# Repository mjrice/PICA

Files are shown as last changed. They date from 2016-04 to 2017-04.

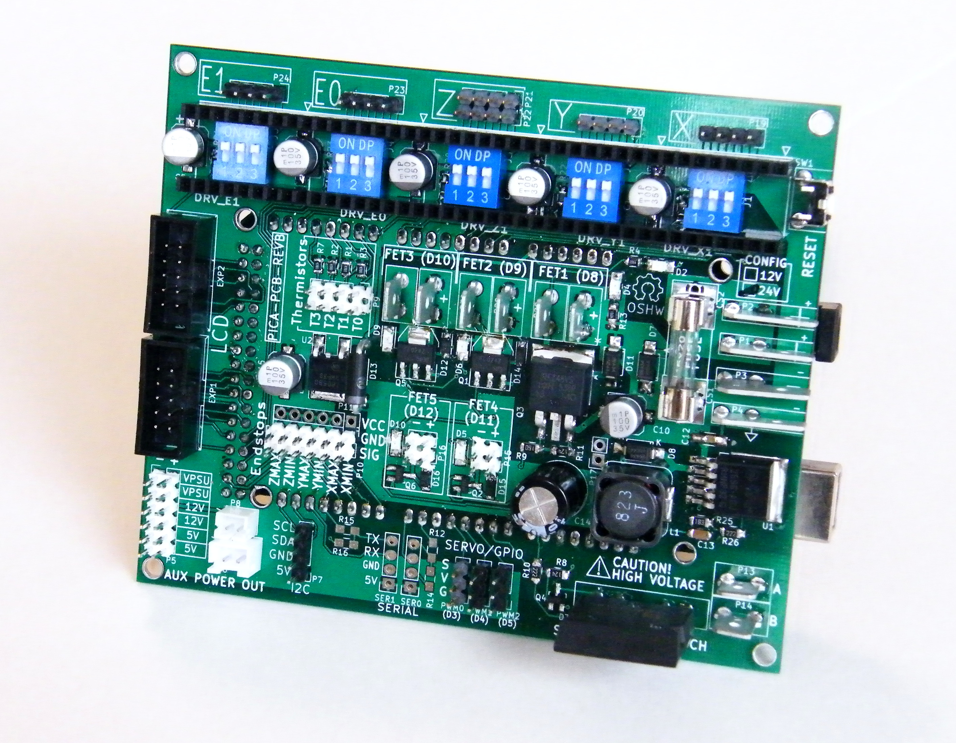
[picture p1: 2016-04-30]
pica-assembled-24v.jpg

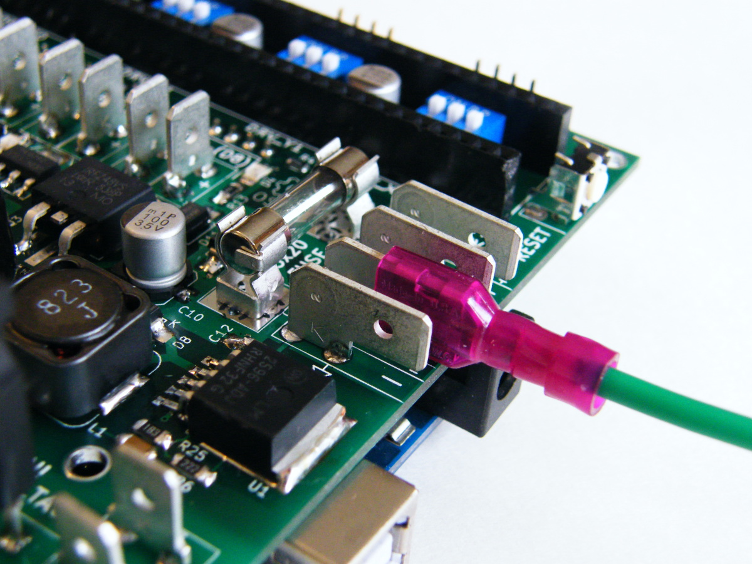
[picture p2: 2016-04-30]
qc.jpg

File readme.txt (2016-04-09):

PICA

Power, Interface, and Control Adapter

An Arduino Mega shield for reprap machines

Based in part on RAMPS by Johnny Russell

Power

* 5x20mm replaceable fuse input 

* 12V to 24V input with on-board 12V buck converter for systems with both 24V and 12V devices

* Five separate MOSFET outputs:

1 High power (15A, up to 24V)
2 Medium power (6A, up to 24V)
2 Low power (2A, 12V)

* Plus 1 SSR output (SPST) capable of 240VAC/5A (more with heatsink)

Monitoring 

* four thermistor inputs
* six endstop inputs

Interface

* LCD interface (SMART LCD controller pinout)
* I2C, 2xSerial, 3xPWM, and auxiliary DC power output connections
* Five Pololu stepper motor driver sockets (A4988 or DRV8825)

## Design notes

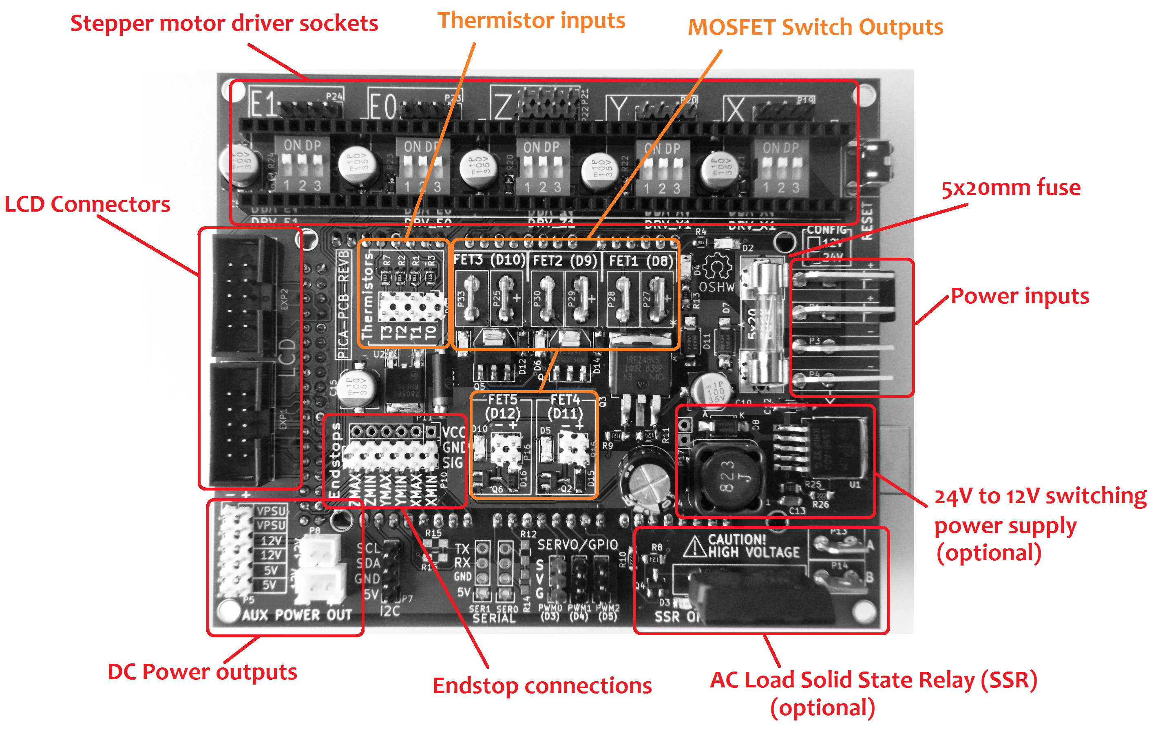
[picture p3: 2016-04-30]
pica-design-layout.png

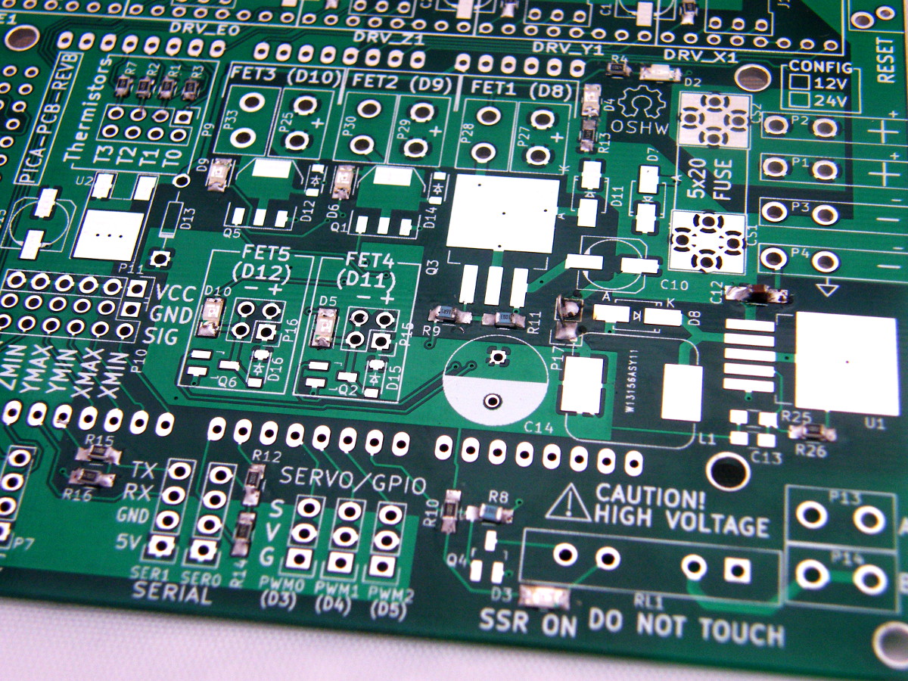
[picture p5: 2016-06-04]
r2k_100k.jpg

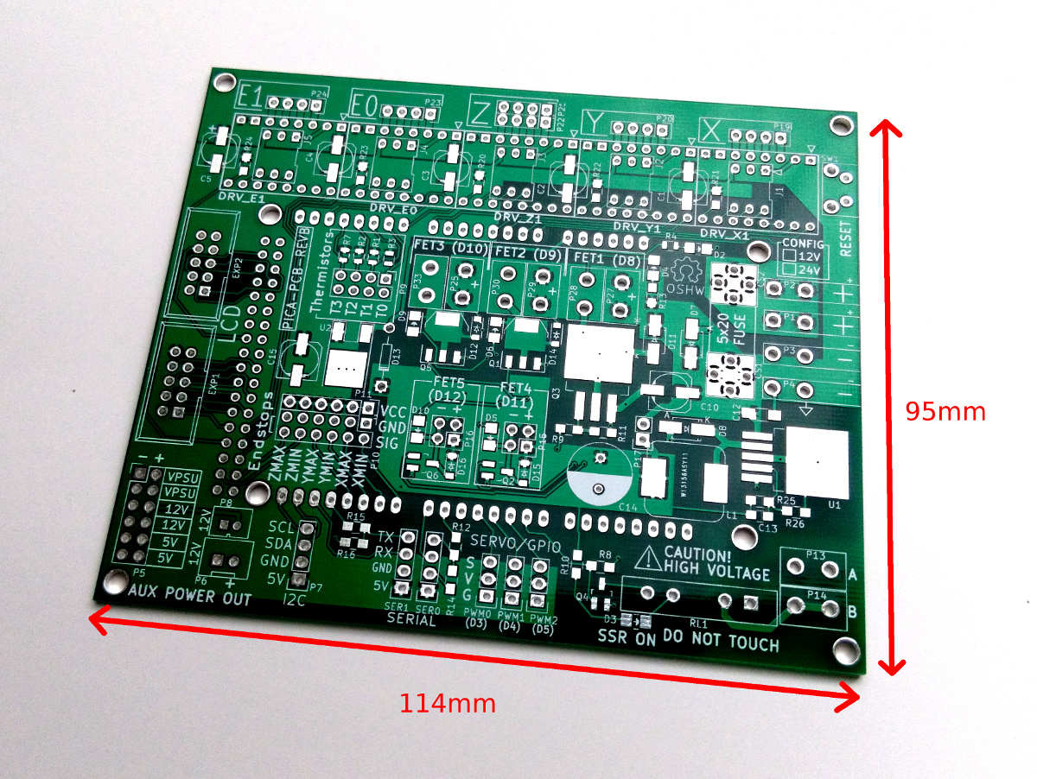
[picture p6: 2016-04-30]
pica-pcb-photo.jpg

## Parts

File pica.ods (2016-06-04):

Parts list, in the recommended order of assembly
Designator | Package | Quantity | Designation | KIT BAG
R13,R20,R21,R22,R23,R24,R14,R16,R4,R5,R6,R1,R2,R3,R7 | R_0805_HandSoldering | 15 | 4.7K | 1
D2 | LED_1206 | 1 | GREEN
D4,D5,D6,D9,D10,D3 | LED_1206 | 6 | Led_Small
RP1 | RESARY_4_CTS_744 | 1 | YC164-JR-0722RL
RP3 | RESARY_4_CTS_744 | 1 | YC164-JR-073K3L
RP2 | RESARY_4_CTS_744 | 1 | YC164-JR-07100KL
 |  |  |  | 2
C6,C7,C8,C9,C11,C12 | C_0805_HandSoldering | 6 | .1UF
R26,R10,R12,R15 | R_0805_HandSoldering | 4 | 2K
R11,R8 | R_0805_HandSoldering | 2 | 100K
 |  |  |  | 3
R9 | R_0805_HandSoldering | 1 | 10
D16,D12,D15,D14 | SOD-123 | 4 | MBR0560
D7,D11 | SMA_Handsoldering | 2 | SS36
 |  |  |  | 4
Q2,Q4,Q6 | SOT-23_Handsoldering | 3 | IRLML6346
Q1,Q5 | SOT-223 | 2 | IRFL024ZPbF
Q3 | TO-263-3Lead | 1 | IRFZ48VS
 |  |  |  | 5
U2 | TO-252-2Lead | 1 | MC7805BDTRKG
C10,C15,C1,C2,C3,C4,C5 | c_elec_6.3x5.8 | 7 | 100UF
J1,J2,J3,J4,J5 | DIP-6_0_ELL | 5 | CONN_02X03
 |  |  |  | 6
DRV_Z1,DRV_X1,DRV_E1,DRV_E0,DRV_Y1 | SWDIP8_.6W | 5 | POLOLU_A4988
EXP1,EXP2 | IDC_Header_Straight_10pins | 2 | CONN_02X05
P11 | Pin_Header_Straight_1x06 | 1 | CONN_01X06
P10,P5 | Pin_Header_Straight_2x06 | 2 | CONN_02X06
P7,P19,P20,P21,P22,P23,P24 | Pin_Header_Straight_1x04 | 7 | CONN_01X04
P9 | Pin_Header_Straight_2x04 | 1 | CONN_02X04
PWM0,PWM1,PWM2 | Pin_Header_Straight_1x03 | 3 | CONN_01X03
P15,P16 | Pin_Header_Straight_1x02 | 2 | CONN_02X02
 |  |  |  | 7
SER0,SER1 | Pin header (female) | 2 | CONN_01X04
SW1 | BSF_RT | 1 | BSF-3100
P17 | Jumper wire | 1
D13 | Diode_Horizontal | 1 | 1N5333
CS1,CS2 | FUSE_CLIP_D_5x20 | 2 | FUSE_CLIP_5x20
P8, P12, P18 | JST_PH_2POS | 3 | JST-PH
P6 | JST_XH_2POS | 1 | JST-XH
SHIELD1 | MEGA_NOLINES | 1 | ARDUINO_MEGA_SHIELD
P28,P27,P29,P30,P25,P33,P13,P14 | SPACE_CONN_VERT | 8 | CONN_01X02 | 8
P2,P1,P3,P4 | SPADE_CONN_RT | 4 | 36-4966-ND

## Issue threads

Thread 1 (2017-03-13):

PICA 24V parts list; Re-ARM compatibility: bridge Vpsu/12V to Vin?

rumlyne, 2017-03-13:
Dear mjrice,

searching for a better alternative than a 24V RAMPS for my Re-ARM board I came across your PICA and I have a few questions:
Are you selling a set of the components needed to make it 24V compatible? If not could you provide a parts list?
Also the PICA provides the Arduino Mega with 9V via the Vin pin. The Re-ARM needs at least 10V and can tolerate up to 30V. Is there a way to bridge that pin to Vpsu/24V or 12V on the Pico? What other electronic parts does the PICOs 9V regulator supply with current? If there are no others it should be easy to bridge the pads reserved for that regulator.

Best regards,
rumlyne

rumlyne, 2017-04-18:
He replied on a different platform:

I sell the boards with or without the 24V input. When it is installed, it
is a buck converter that generates an on-board 12V from the 24V. The 12V
is used to power the two lower power mosfet switches as well as the
on-board 5V regulator and the arduino itself through a zener diode. The
three higher power mosfet switches and the stepper motor drivers are driven
from the input supply directly. You can also modify a 12V unit to be 24V
compatible - the design is all open source and the schematic is here:
https://github.com/mjrice/PICA/blob/master/pica_schematic.pdf

And lastly to answer your question, yes, you could either short out or
reverse the diode D13 which would increase the voltage on the arduino's VIN
pin from 9V to about 11.3V.

I don't know much about the Re-arm board but otherwise it looks like it
should work like you expect.

Closed 2017-04-18.

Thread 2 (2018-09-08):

No 5V (VCC) on the shield

Duckle29, 2018-09-08:
Hey there. I'm flipping through the board and schematic (in kicad) and I can't figure out where the shield gets 5v from

It seems that the shields 12v is separate from U2, which should generate the onboard 5v. The only way I can see this working, is if the arduino is powered through it's barrel-jack, and then this voltage is passed to the shield via the megas VIN pin, why not use the on-board 12v source, or at least offer a power selector jumper?

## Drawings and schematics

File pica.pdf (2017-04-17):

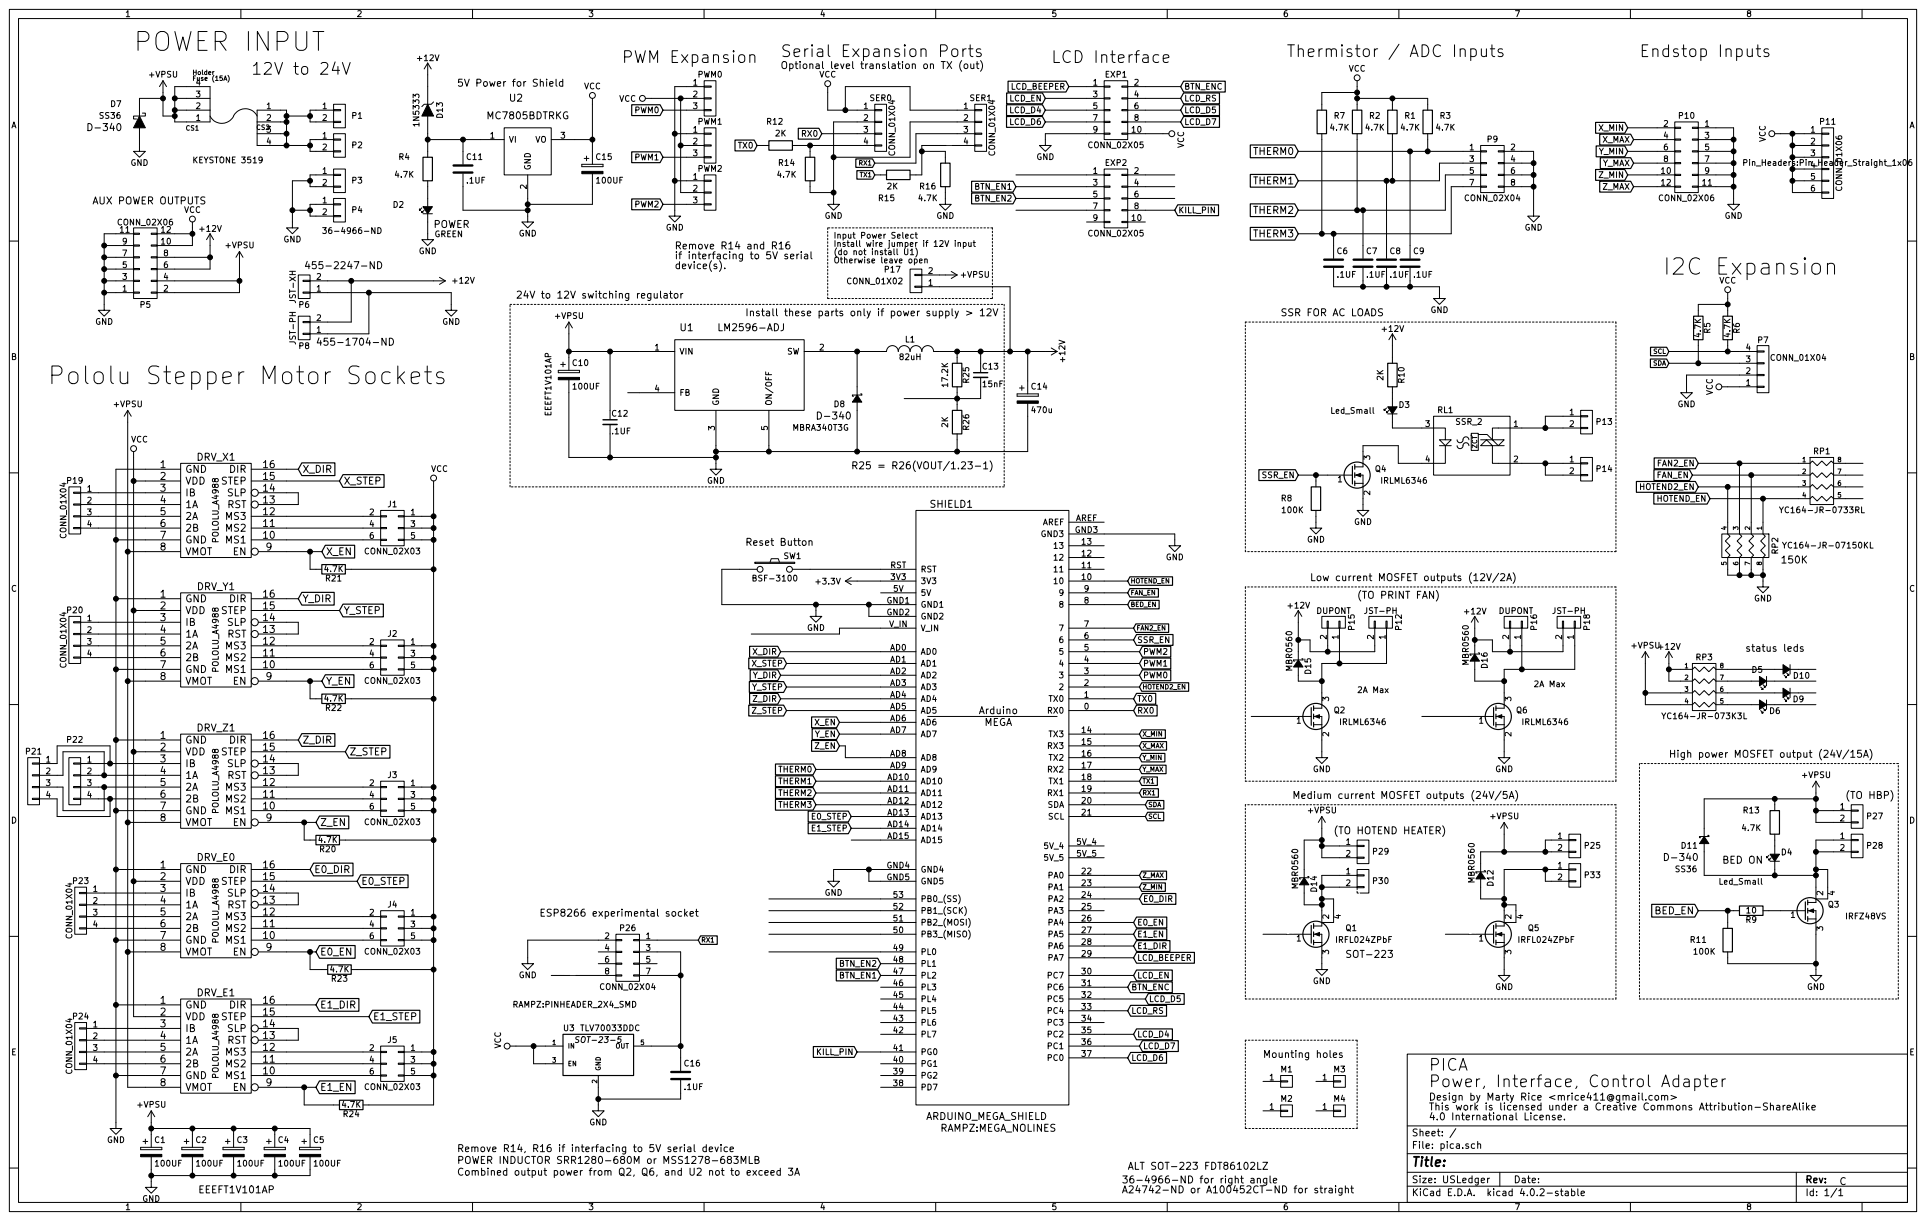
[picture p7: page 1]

+3.3V Serial Expansion Ports
4.7KGND Optional level translation on TX (out)
3PWM0 GND

Input Power Select
Install wire jumper if 12V input
(do not install U1)

if interfacing to 5V serial

status leds 24V to 12V switching regulator

Install these parts only if power supply > 12V

4 RL1 SSR_2 D3 Led_Small SSR FOR AC LOADS

Pololu Stepper Motor Sockets

High power MOSFET output (24V/15A) 150K

Medium current MOSFET outputs (24V/5A)

PICA
Power, Interface, Control Adapter
Design by Marty Rice <mrice411@gmail.com>
This work is licensed under a Creative Commons Attribution-ShareAlike 4.0 International License.

File: pica.sch Sheet: /

Remove R14, R16 if interfacing to 5V serial device
POWER INDUCTOR SRR1280-680M or MSS1278-683MLB
Combined output power from Q2, Q6, and U2 not to exceed 3A

ALT SOT-223 FDT86102LZ
36-4966-ND for right angle
A24742-ND or A100452CT-ND for straight

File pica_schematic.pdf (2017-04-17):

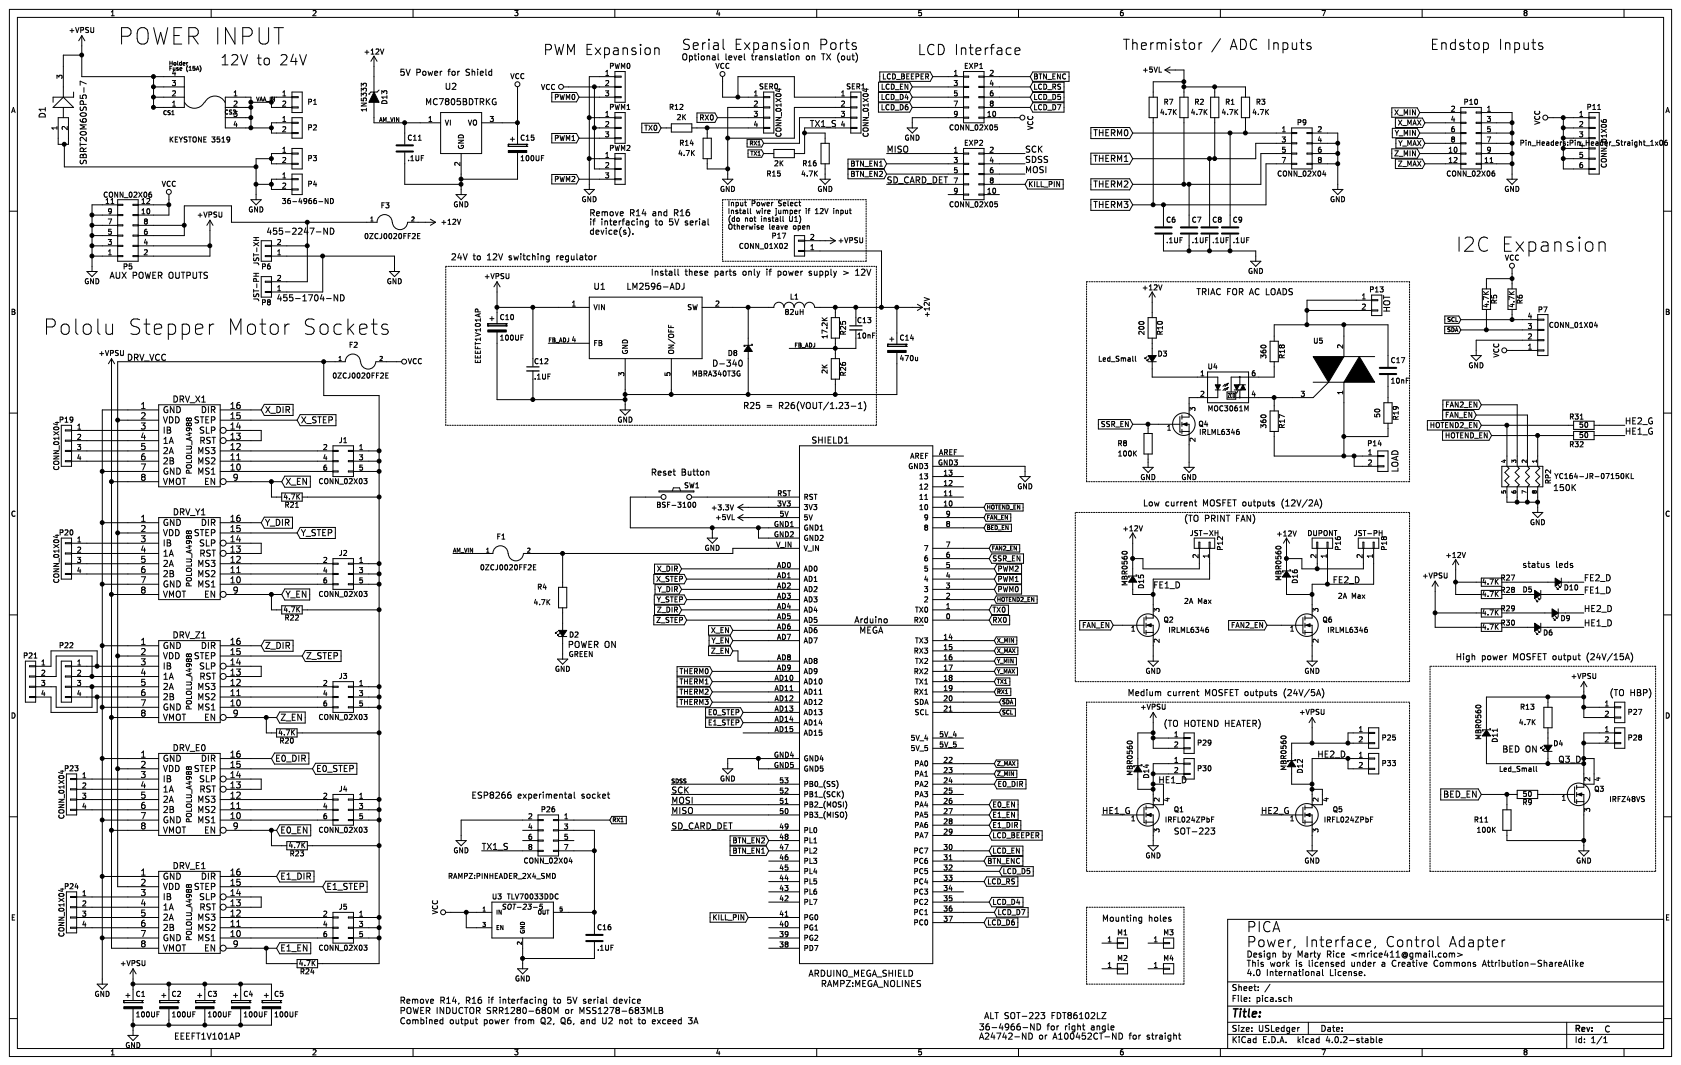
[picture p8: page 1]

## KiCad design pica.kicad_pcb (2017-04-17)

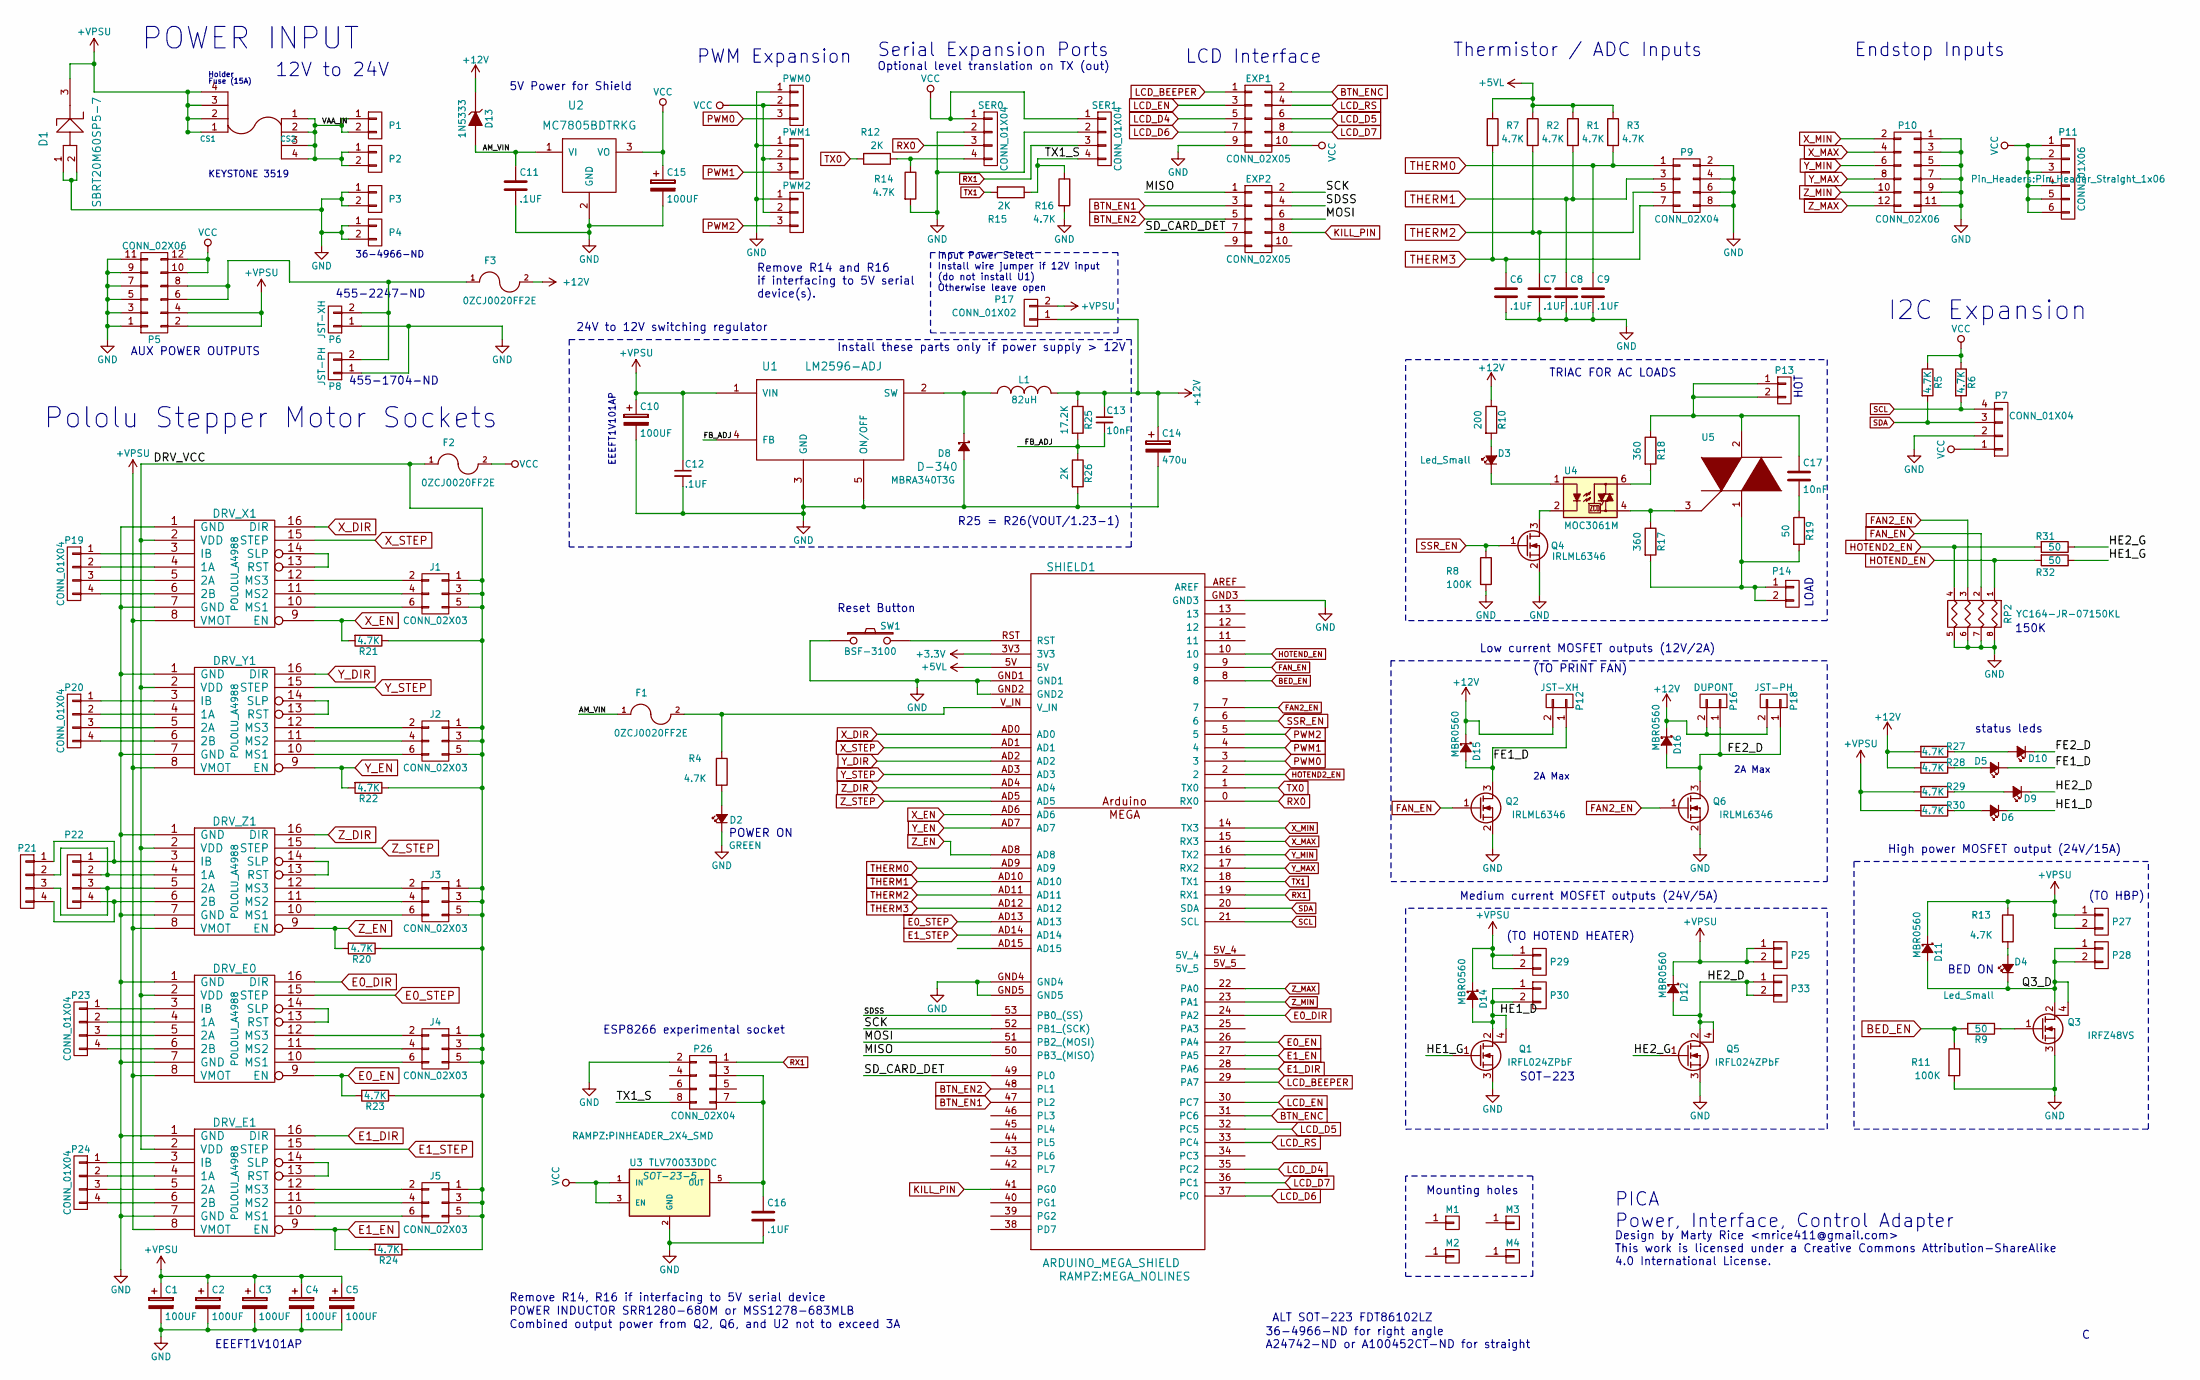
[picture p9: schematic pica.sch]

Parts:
C1, C2, C3, C4, C5, C10, C15: 100UF; c_elec_6.3x5.8
C6, C7, C8, C9, C11, C12, C16: .1UF; C_0805_HandSoldering
C13, C17: 10nF; C_1206_HandSoldering
C14: 470u; C_Radial_D10_L13_P5
CS1, CS2: FUSE_CLIP_5x20; FUSE_CLIP_D_5x20
D1: SBRT20M60SP5-7; POWERDI5
D2: GREEN; LED_1206
D3, D4, D5, D6, D9, D10: Led_Small; LED_1206
D8: MBRA340T3G; SMA_Handsoldering
D11, D12, D14, D15, D16: MBR0560; SOD-123
D13: 1N5333; Diode_Horizontal
DRV_E0, DRV_E1: POLOLU_A4988; SWDIP8_.6W
DRV_X1: POLOLU_A4988; SWDIP8_.6W
DRV_Y1: POLOLU_A4988; SWDIP8_.6W
DRV_Z1: POLOLU_A4988; SWDIP8_.6W
EXP1, EXP2: CONN_02X05; IDC_Header_Straight_10pins_DUAL
F1, F2, F3: 0ZCJ0020FF2E; Fuse_SMD1206_Wave
J1, J2, J3, J4, J5: CONN_02X03; DIP-6_0_ELL
L1: 82uH; RH127
M1, M2, M3, M4: CONN_01X01; MHOLE125
P1, P2, P3, P4: 36-4966-ND; SPADE_CONN_RT
P5, P10: CONN_02X06; Pin_Header_Straight_2x06
P6, P12: JST-XH; JST_XH_2POS
P7, P19, P20, P21, P22, P23, P24: CONN_01X04; Pin_Header_Straight_1x04
P8, P18: JST-PH; JST_PH_2POS
P9: CONN_02X04; Pin_Header_Straight_2x04
P11: CONN_01X06; Pin_Header_Straight_1x06
P13, P14, P25, P27, P28, P29, P30, P33: CONN_01X02; SPACE_CONN_VERT
P16: DUPONT; Pin_Header_Straight_1x02
P17: CONN_01X02; Pin_Header_Straight_1x02
P26: CONN_02X04; PINHEADER_2X4_SMD
PWM0, PWM1, PWM2: CONN_01X03; Pin_Header_Straight_1x03
Q1, Q5: IRFL024ZPbF; SOT-223
Q2, Q4, Q6: IRLML6346; SOT-23_Handsoldering
Q3: IRFZ48VS; TO-263-3Lead
R1, R2, R3, R4, R5, R6, R7, R13, R14, R16, R20, R21, R22, R23, R24, R27, R28, R29, R30: 4.7K; R_0805_HandSoldering
R8, R11: 100K; R_0805_HandSoldering
R9, R19, R31, R32: 50; R_0805_HandSoldering
R10: 200; R_0805_HandSoldering
R12, R15, R26: 2K; R_0805_HandSoldering
R17, R18: 360; R_0805_HandSoldering
R25: 17.2K; R_0805_HandSoldering
RP2: YC164-JR-07150KL; RESARY_4_CTS_744
SER0, SER1: CONN_01X04; Pin_Header_Straight_1x04
SHIELD1: ARDUINO_MEGA_SHIELD; MEGA_NOLINES
SW1: BSF-3100; BSF_RT
U1: LM2596-ADJ; TO-263-5Lead
U2: MC7805BDTRKG; TO-252-2Lead
U3: TLV70033DDC; SOT-23-5
U4: MOC3061M; 6SMD
U5: TRIAC; TO-252-2Lead

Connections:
+3V3: SHIELD1.3V3
+5VL: R1.1, R2.1, R3.1, R7.1, SHIELD1.5V
+12V: C13.1, C14.1, D13.1 (K), D15.1 (K), D16.1 (K), F3.2, L1.2, P12.2, P16.2, P17.1, P18.2, R10.1, R25.1, R27.2, R28.2
+VPSU: C1.1, C2.1, C3.1, C4.1, C5.1, C10.1, C12.1, CS1.1, CS1.2, CS1.3, CS1.4, D1.3, D11.1 (K), D12.1 (K), D14.1 (K), DRV_E0.8 (VMOT), DRV_E1.8 (VMOT), DRV_X1.8 (VMOT), DRV_Y1.8 (VMOT), DRV_Z1.8 (VMOT), P5.2, P5.4, P17.2, P25.1, P25.2, P27.1, P27.2, P29.1, P29.2, R13.1, R29.2, R30.2, U1.1 (VIN)
/AM_VIN: C11.1, D13.2 (A), F1.1, U2.1 (VI)
/DRV_VCC: DRV_E0.2 (VDD), DRV_E1.2 (VDD), DRV_X1.2 (VDD), DRV_Y1.2 (VDD), DRV_Z1.2 (VDD), F2.1, J1.1, J1.3, J1.5, J2.1, J2.3, J2.5, J3.1, J3.3, J3.5, J4.1, J4.3, J4.5, J5.1, J5.3, J5.5, R20.1, R21.1, R22.1, R23.1, R24.1
/FB_ADJ: C13.2, R25.2, R26.1, U1.4 (FB)
/FE1_D: D5.1 (K), D15.2 (A), P12.1, Q2.3 (D)
/FE2_D: D10.1 (K), D16.2 (A), P16.1, P18.1, Q6.3 (D)
/HE1_D: D6.1 (K), D14.2 (A), P30.1, P30.2, Q1.2 (D), Q1.4 (D)
/HE1_G: Q1.1 (G), R32.1
/HE2_D: D9.1 (K), D12.2 (A), P33.1, P33.2, Q5.2 (D), Q5.4 (D)
/HE2_G: Q5.1 (G), R31.1
/MISO: EXP2.1, SHIELD1.50 (PB3_(MISO))
/MOSI: EXP2.6, SHIELD1.51 (PB2_(MOSI))
/Q3_D: D4.1 (K), D11.2 (A), P28.1, P28.2, Q3.2 (D), Q3.4 (D)
/SCK: EXP2.2, SHIELD1.52 (PB1_(SCK))
/SDSS: EXP2.4, SHIELD1.53 (PB0_(SS))
/SD_CARD_DET: EXP2.7, SHIELD1.49 (PL0)
/TX1_S: P26.8, R15.1, R16.1, SER1.4
/VAA_IN: CS2.1, CS2.2, CS2.3, CS2.4, P1.1, P1.2, P2.1, P2.2
BED_EN: R9.2, R11.1, SHIELD1.8
BTN_EN1: EXP2.3, SHIELD1.47 (PL2)
BTN_EN2: EXP2.5, SHIELD1.48 (PL1)
BTN_ENC: EXP1.2, SHIELD1.31 (PC6)
E0_DIR: DRV_E0.16 (DIR), SHIELD1.24 (PA2)
E0_EN: DRV_E0.9 (EN), R23.2, SHIELD1.26 (PA4)
E0_STEP: DRV_E0.15 (STEP), SHIELD1.AD13
E1_DIR: DRV_E1.16 (DIR), SHIELD1.28 (PA6)
E1_EN: DRV_E1.9 (EN), R24.2, SHIELD1.27 (PA5)
E1_STEP: DRV_E1.15 (STEP), SHIELD1.AD14
FAN2_EN: Q6.1 (G), RP2.3, SHIELD1.7
FAN_EN: Q2.1 (G), RP2.2, SHIELD1.9
GND: C1.2, C2.2, C3.2, C4.2, C5.2, C6.2, C7.2, C8.2, C9.2, C10.2, C11.2, C12.2, C14.2, C15.2, C16.2, D1.1, D1.2, D2.1 (K), D8.2 (A), DRV_E0.1 (GND), DRV_E0.7 (GND), DRV_E1.1 (GND), DRV_E1.7 (GND), DRV_X1.1 (GND), DRV_X1.7 (GND), DRV_Y1.1 (GND), DRV_Y1.7 (GND), DRV_Z1.1 (GND), DRV_Z1.7 (GND), EXP1.9, P3.1, P3.2, P4.1, P4.2, P5.1, P5.3, P5.5, P5.7, P5.9, P5.11, P6.1, P7.2, P8.1, P9.2, P9.4, P9.6, P9.8, P10.1, P10.3, P10.5, P10.7, P10.9, P10.11, P26.2, PWM0.1, PWM1.1, PWM2.1, Q1.3 (S), Q2.2 (S), Q3.3 (S), Q4.2 (S), Q5.3 (S), Q6.2 (S), R8.2, R11.2, R14.2, R16.2, R26.2, RP2.5 (R4), RP2.6 (R3), RP2.7 (R2), RP2.8 (R1), SER0.2, SER1.2, SHIELD1.GND1, SHIELD1.GND2, SHIELD1.GND3, SHIELD1.GND4, SHIELD1.GND5, SW1.1, U1.3 (GND), U1.5 (ON/OFF), U2.2 (GND), U3.2 (GND)
HOTEND2_EN: R31.2, RP2.4, SHIELD1.2
HOTEND_EN: R32.2, RP2.1, SHIELD1.10
KILL_PIN: EXP2.8, SHIELD1.41 (PG0)
LCD_BEEPER: EXP1.1, SHIELD1.29 (PA7)
LCD_D4: EXP1.5, SHIELD1.35 (PC2)
LCD_D5: EXP1.6, SHIELD1.32 (PC5)
LCD_D6: EXP1.7, SHIELD1.37 (PC0)
LCD_D7: EXP1.8, SHIELD1.36 (PC1)
LCD_EN: EXP1.3, SHIELD1.30 (PC7)
LCD_RS: EXP1.4, SHIELD1.33 (PC4)
unnamed: C16.1, P26.3, P26.7, U3.5 (OUT)
unnamed: C17.1, P13.1, P13.2, R18.1, U5.2
unnamed: C17.2, R19.1
unnamed: D2.2 (A), R4.2
unnamed: D3.1 (K), U4.1
unnamed: D3.2 (A), R10.2
unnamed: D4.2 (A), R13.2
unnamed: D5.2 (A), R28.1
unnamed: D6.2 (A), R30.1
unnamed: D8.1 (K), L1.1, U1.2 (SW)
unnamed: D9.2 (A), R29.1
unnamed: D10.2 (A), R27.1
unnamed: DRV_E0.3 (IB), P23.1
unnamed: DRV_E0.4 (1A), P23.2
unnamed: DRV_E0.5 (2A), P23.3
unnamed: DRV_E0.6 (2B), P23.4
unnamed: DRV_E0.10 (MS1), J4.6
unnamed: DRV_E0.11 (MS2), J4.4
unnamed: DRV_E0.12 (MS3), J4.2
unnamed: DRV_E0.13 (RST), DRV_E0.14 (SLP)
unnamed: DRV_E1.3 (IB), P24.1
unnamed: DRV_E1.4 (1A), P24.2
unnamed: DRV_E1.5 (2A), P24.3
unnamed: DRV_E1.6 (2B), P24.4
unnamed: DRV_E1.10 (MS1), J5.6
unnamed: DRV_E1.11 (MS2), J5.4
unnamed: DRV_E1.12 (MS3), J5.2
unnamed: DRV_E1.13 (RST), DRV_E1.14 (SLP)
unnamed: DRV_X1.3 (IB), P19.1
unnamed: DRV_X1.4 (1A), P19.2
unnamed: DRV_X1.5 (2A), P19.3
unnamed: DRV_X1.6 (2B), P19.4
unnamed: DRV_X1.10 (MS1), J1.6
unnamed: DRV_X1.11 (MS2), J1.4
unnamed: DRV_X1.12 (MS3), J1.2
unnamed: DRV_X1.13 (RST), DRV_X1.14 (SLP)
unnamed: DRV_Y1.3 (IB), P20.1
unnamed: DRV_Y1.4 (1A), P20.2
unnamed: DRV_Y1.5 (2A), P20.3
unnamed: DRV_Y1.6 (2B), P20.4
unnamed: DRV_Y1.10 (MS1), J2.6
unnamed: DRV_Y1.11 (MS2), J2.4
unnamed: DRV_Y1.12 (MS3), J2.2
unnamed: DRV_Y1.13 (RST), DRV_Y1.14 (SLP)
unnamed: DRV_Z1.3 (IB), P21.1, P22.1
unnamed: DRV_Z1.4 (1A), P21.2, P22.2
unnamed: DRV_Z1.5 (2A), P21.3, P22.3
unnamed: DRV_Z1.6 (2B), P21.4, P22.4
unnamed: DRV_Z1.10 (MS1), J3.6
unnamed: DRV_Z1.11 (MS2), J3.4
unnamed: DRV_Z1.12 (MS3), J3.2
unnamed: DRV_Z1.13 (RST), DRV_Z1.14 (SLP)
unnamed: F1.2, R4.1, SHIELD1.V_IN
unnamed: F3.1, P5.6, P5.8, P6.2, P8.2
unnamed: P14.1, P14.2, R17.2, R19.2, U5.1
unnamed: Q3.1 (G), R9.1
unnamed: Q4.3 (D), U4.2
unnamed: R12.1, R14.1, SER0.4
unnamed: R17.1, U4.4, U5.3
unnamed: R18.2, U4.6
unnamed: SHIELD1.RST, SW1.2
PWM0: PWM0.3, SHIELD1.3
PWM1: PWM1.3, SHIELD1.4
PWM2: PWM2.3, SHIELD1.5
RX0: SER0.3, SHIELD1.0 (RX0)
RX1: P26.1, SER1.3, SHIELD1.19 (RX1)
SCL: P7.4, R6.2, SHIELD1.21 (SCL)
SDA: P7.3, R5.2, SHIELD1.20 (SDA)
SSR_EN: Q4.1 (G), R8.1, SHIELD1.6
THERM0: C9.1, P9.1, R3.2, SHIELD1.AD9
THERM1: C8.1, P9.3, R1.2, SHIELD1.AD10
THERM2: C7.1, P9.5, R2.2, SHIELD1.AD11
THERM3: C6.1, P9.7, R7.2, SHIELD1.AD12
TX0: R12.2, SHIELD1.1 (TX0)
TX1: R15.2, SHIELD1.18 (TX1)
VCC: C15.1, EXP1.10, F2.2, P5.10, P5.12, P7.1, P11.1, P11.2, P11.3, P11.4, P11.5, P11.6, PWM0.2, PWM1.2, PWM2.2, R5.1, R6.1, SER0.1, SER1.1, U2.3 (VO), U3.1 (IN), U3.3 (EN)
X_DIR: DRV_X1.16 (DIR), SHIELD1.AD0
X_EN: DRV_X1.9 (EN), R21.2, SHIELD1.AD6
X_MAX: P10.4, SHIELD1.15 (RX3)
X_MIN: P10.2, SHIELD1.14 (TX3)
X_STEP: DRV_X1.15 (STEP), SHIELD1.AD1
Y_DIR: DRV_Y1.16 (DIR), SHIELD1.AD2
Y_EN: DRV_Y1.9 (EN), R22.2, SHIELD1.AD7
Y_MAX: P10.8, SHIELD1.17 (RX2)
Y_MIN: P10.6, SHIELD1.16 (TX2)
Y_STEP: DRV_Y1.15 (STEP), SHIELD1.AD3
Z_DIR: DRV_Z1.16 (DIR), SHIELD1.AD4
Z_EN: DRV_Z1.9 (EN), R20.2, SHIELD1.AD8
Z_MAX: P10.12, SHIELD1.22 (PA0)
Z_MIN: P10.10, SHIELD1.23 (PA1)
Z_STEP: DRV_Z1.15 (STEP), SHIELD1.AD5

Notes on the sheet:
POWER INPUT
(TO HBP)
(TO PRINT FAN)
(TO HOTEND HEATER)
EEEFT1V101AP
POWER ON
BED ON
I2C Expansion
Holder
Fuse (15A)
Endstop Inputs
Thermistor / ADC Inputs
LCD Interface
Pololu Stepper Motor Sockets
2A Max
Serial Expansion Ports
PICA Power, Interface, Control Adapter
12V to 24V
PWM Expansion
Input Power Select Install wire jumper if 12V input (do not install U1) Otherwise leave open
36-4966-ND
SOT-223
Low current MOSFET outputs (12V/2A)
36-4966-ND for right angle A24742-ND or A100452CT-ND for straight
Medium current MOSFET outputs (24V/5A)
High power MOSFET output (24V/15A)
150K
AUX POWER OUTPUTS
ALT SOT-223 FDT86102LZ
TRIAC FOR AC LOADS
Mounting holes
Combined output power from Q2, Q6, and U2 not to exceed 3A
Reset Button
5V Power for Shield
status leds
24V to 12V switching regulator
R25 = R26(VOUT/1.23-1)
Install these parts only if power supply > 12V
POWER INDUCTOR SRR1280-680M or MSS1278-683MLB
Optional level translation on TX (out)

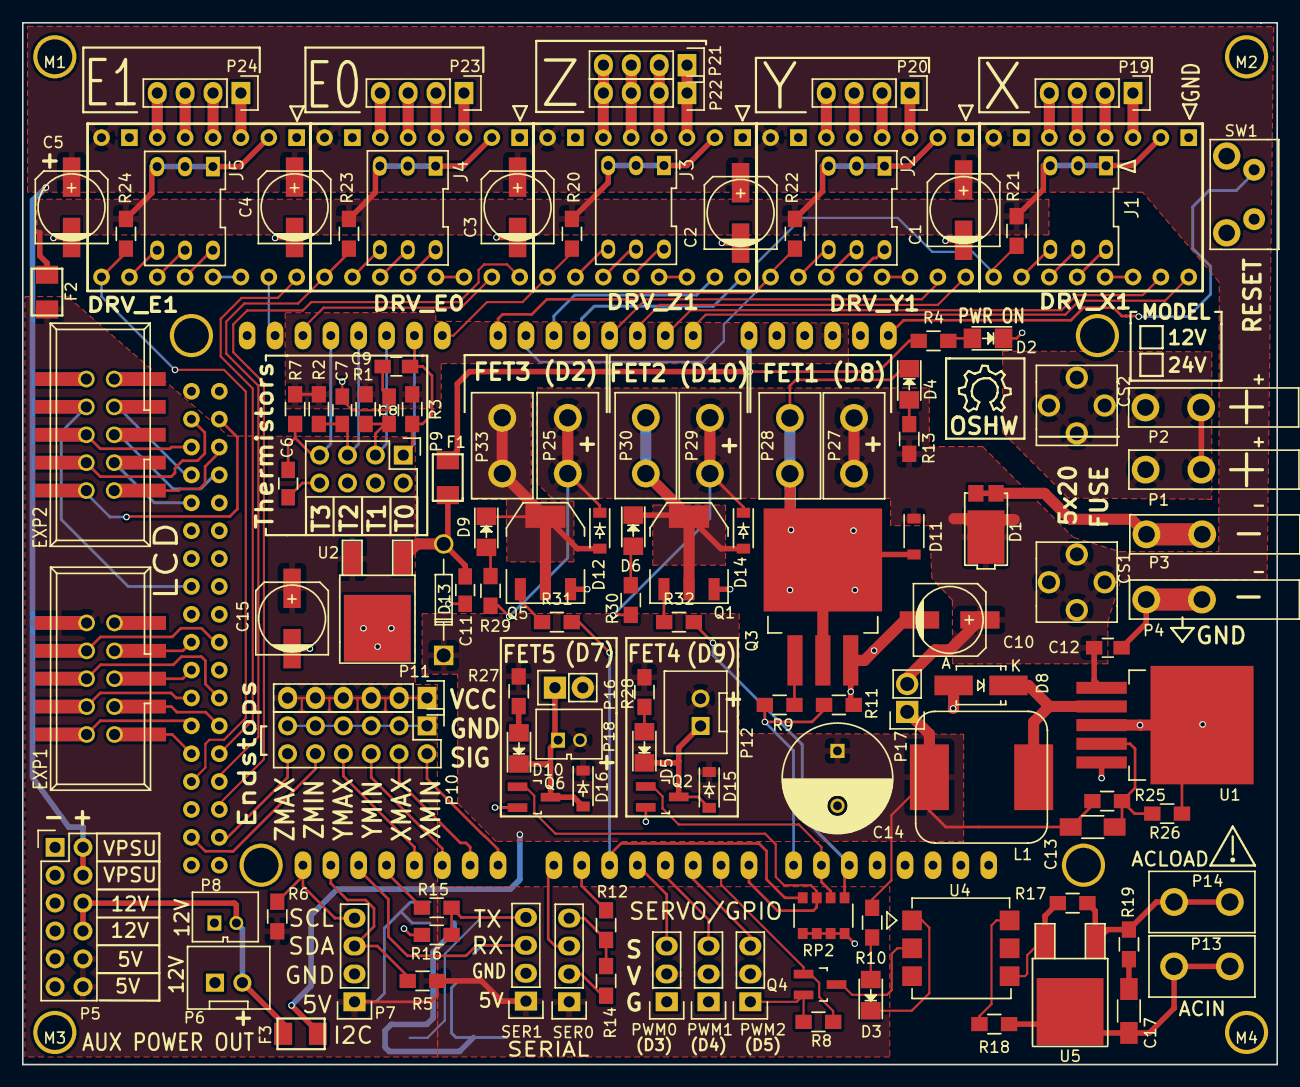
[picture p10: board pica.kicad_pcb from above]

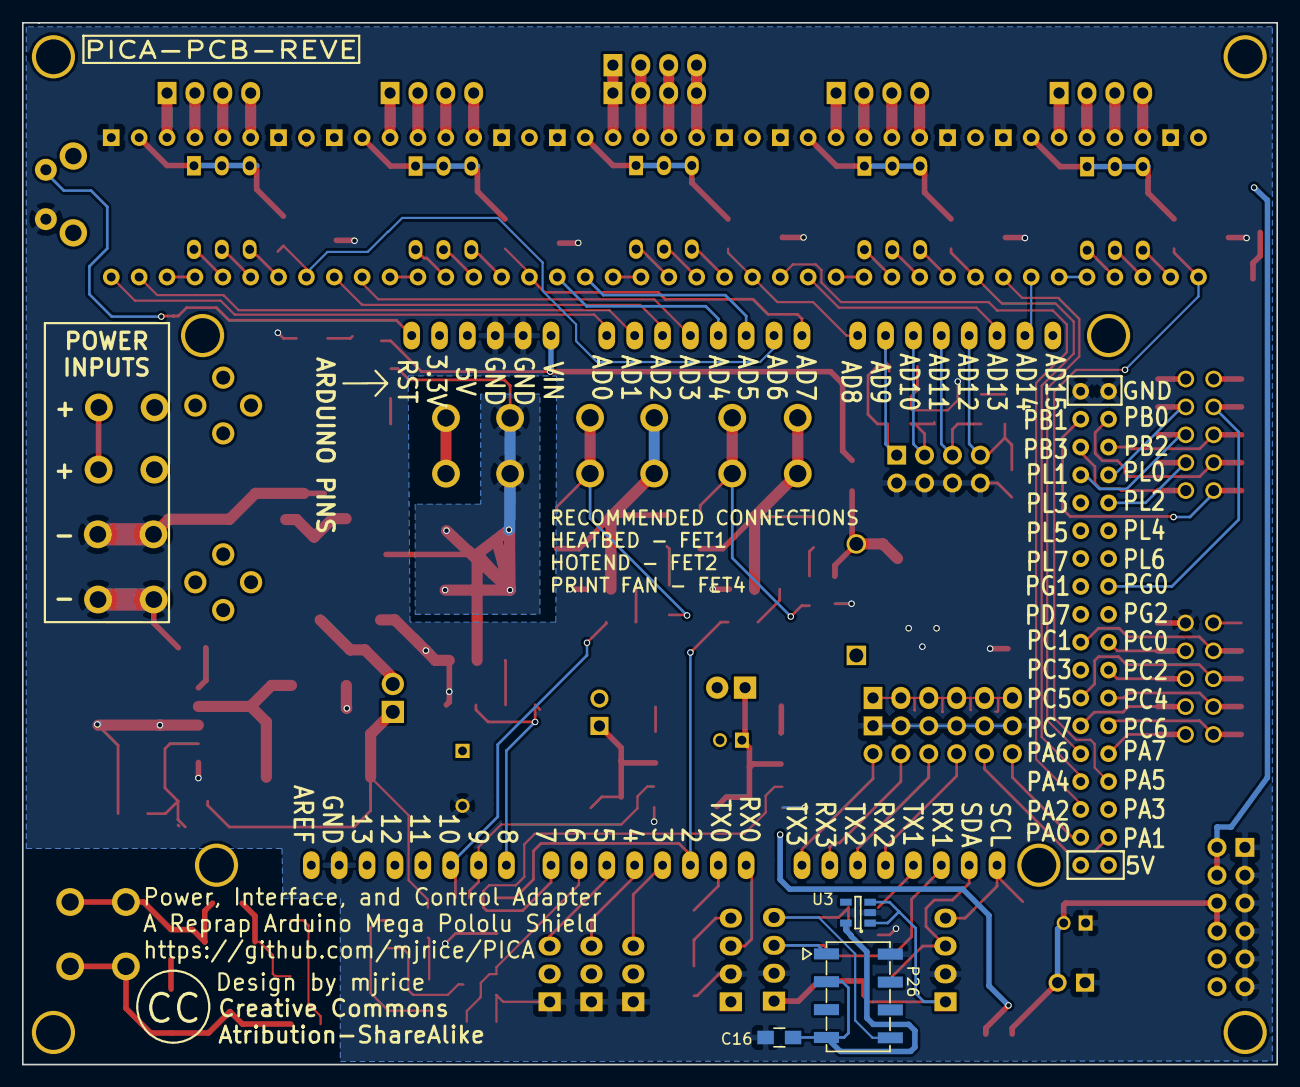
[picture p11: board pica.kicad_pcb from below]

Board: 2 copper layers, 114.3 x 94.9 mm, 135 parts (3 on the bottom side), 134 nets.

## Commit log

2016-04-09 added pdf of schematic
    [pica.sch]
2016-04-09 added png image of the board layout
    [pica.kicad_pcb]
2016-04-30 rev b
    [pica-B.Cu.gbr, pica-B.Mask.gbr, pica-B.SilkS.gbr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]
2016-05-26 added assembly guide
2016-06-04 Final rev C design files
    [pica-B.Cu.gbr, pica-B.Mask.gbr, pica-B.SilkS.gbr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]
2017-01-24 assembly guide for rev C
2017-04-17 update rev e files
    [pica-B.Cu.gbr, pica-B.Mask.gbr, pica-B.SilkS.gbr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]
